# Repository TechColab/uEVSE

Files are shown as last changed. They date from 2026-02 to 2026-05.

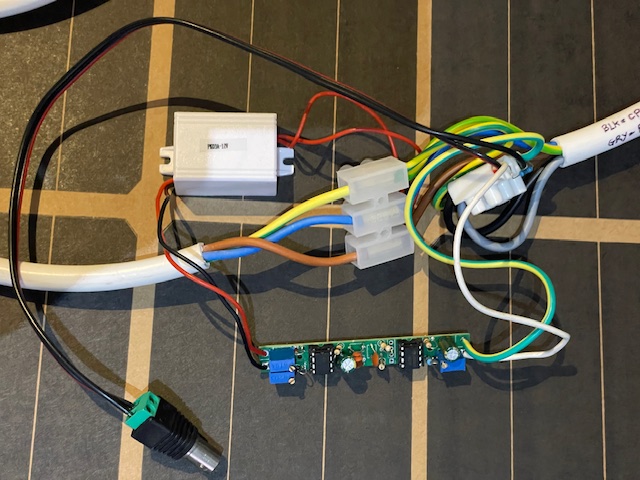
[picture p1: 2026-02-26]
EVSE-components.JPG

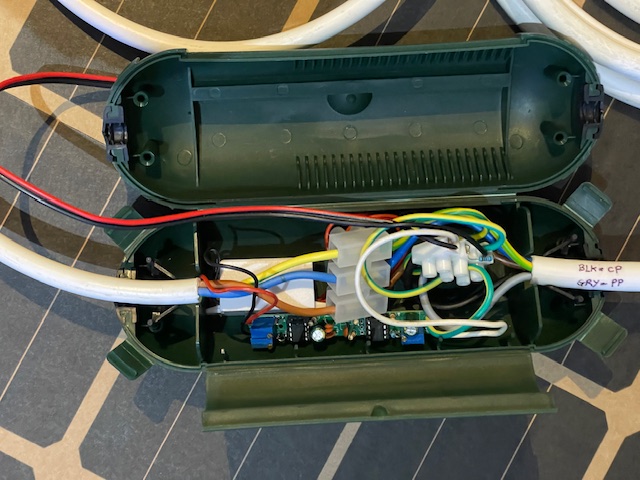
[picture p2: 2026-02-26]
InlineEnclosure.JPG

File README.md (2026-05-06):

# uEVSE or dumb little charger
The minimally viable Electric Vehicle Supply Equipment. Mostly out of curiocity but also as a reaction to the relatively high prices of the cheapest available "Granny charger" products that might be your first step when charging your first BEV.  

In my exploration, the highest unavoidable component costs are the power cable and special connectors. You won't have much choice for the connectors and you really shouldn't compromise on the power cable either. When comparing prices, be sure they are the length you need with a safe amount of slack.  

I've seen quite a few Arduino based DIY EVSE projects but that still has an entry-level threshold of complexity that might put some people off. And I was confident I could make something better - in terms of minimalism.  

Staring with the excellent work by Julian Ilett (JI) at https://www.youtube.com/watch?v=wdK0bfTGi6M&t=7s and other videos, I wanted to address the two biggest issues standing in the way of further simplification.  

The CP (Control Pilot) signal needs to be +/-12V or 24V peak-to-peak.  
In the above example this is acheived with a pair of small 12V batteries which you won't find in your local supermarket. 
Some others have used a dual output PSU with +12V & +5V for the electronics, with a DC-DC converter to generate -12V. 
Another example used 3 separate PSUs.  

I have used a single 12V PSU with the output swing acheived by an H-bridge configuration. 
This takes advantage of the fact that the PE (Protective Earth) of the car & the Earth from the mains, are not related to the 0V power rail of the electonics. This does mean than a fully isolated PSU is an ABSOLUTE requirement but it should be anyway. 
In practice, I bought the 3 cheapest different designs of 12V PSU modules from AliExpress and all were good enough. Two were under GBP 2.00  

The CP signal also needs to follow a multi-stage protocol sequence to make the car happy enough to start drawing current.  
As JI noted, his car was pretty tolerant of the sequence and a definitive specification for the timing of the sequence stages cannot be found online anyway. This made me wonder how much more of the protocol sequence could be skipped. 
I have since succeded without a microcontroller at all, using just a 555 timer & an op-amp with a few resistors & capacitors. 

## Design decisions  
I quickly decided I was going to follow two different paths - the pure minimal and the feature-ritch minimal in the same project. The goals for this version are:  
Drop the option for vented charging such as AGM batteries in golf buggies.  
Cheapest possible entry level that delivers the minimum viable function.  
Fixed output at a modest rate no more than 10A.  
Must connect to car before mains and disconnect mains before car.  
An upgrade path that doesn't waste earlier purchases.  
Not an end product but a kit to educate, and for those willing, form the base of their own functioning DIY EVSE.  

## Experimental evolution  
Following the spec. at  https://en.wikipedia.org/wiki/SAE_J1772  my first thought regarding the 1kHz CP signal was that "you could probably do that with a 555" as it can run directly from 12V. 
I calculated that the maximum current needed from the CP signal is less than 20mA, if we drop the vented charging option. This is within the capability of an NE555P timer chip. But that only has one output when I need a complimentary pair of outputs to get a 24V swing from the 12V supply. A single buffer transistor wouldn't do as the output needs to both sink and source 20mA. I settled on using a cheap op-amp that suits.  

The H-bridge output worked fine on my oscilloscope so I moved on to the next issue of duty cycle. I've never explored the duty-cycle quirks of the 555 so I did some research and found a circuit which allows extreme adjustment from 5 to 95% while also solving the issue of maintaining the frequency while adjusting the duty-cycle. I selected passive components and trim-pots for frequence & duty.  

The first experiments with my car took a bit of manual fidelity but worked in both getting the car to draw some current and learning about the car's protocol expectations. Specifically:  
It did pay attention to the PP (Proximity Pilot) resistor being there (as JI found).  
It didn't seem to care if the mains was presented too early (as JI found).  
It didn't seem to like the 1kHz CP signal being present from the start.  
It does respond to the duty cycle as expected.  
I would like to find the minimum duty cycle the car will work at but I haven't yet.  
I did find that if the duty cycle is accidentally inverted, the 87% presented will cause the car to draw more than enough to trip my home battery before blowing the 13A fuse in the mains plug.  If you're in a country where the mains plugs don't include a fuse, take appropriate precautions.  

While waiting for the special conectors to arrive from China, I bought the cheapest EVSE product I could find which included a timer function to make use of my over-night tariff. Disappointingly it can set a delay or a duration but not both. I later discovered that after a power-loss, it will return to the last used charge current and carry on. So I tried it via a Smart-switch rated at 16A and found it works fine with a schedule configred from the mobile app. I could have bought an EVSE without the built-in timer function. In fact this is the key to the cost-efficient upgrate path.  

By looking at the signals from the bought EVSE on my oscilloscope, I thought my circuit probably needed the CP to be held at 12V+ for an initiual period before starting the 1kHz square wave. As I used an LM358 dual op-amp chip, I could use the spare to hold the 555 in reset until a capacitor charged through a resistor, giving a couple of seconds delay. This breadboard prototype sucesfully got the car to draw a controlled amount of current shortly after boot. Proof of concept!  

As an early experiment for the feature-ritch varient, I also tried it with a 4428 driver IC to see if that would help square-off the rather imperfect signal edges. It didn't make much difference but the driver got rather hot. This was a dual complimentary pair package where I was initially driving both inputs from the 555 so they had a brief cross-over period. I later tried a 4423/4424 dual matched pair package where one was driven from the 555 and the other from the output of the op-amp inverter whose propogation delay was enough to avoid the over-lap heating.  

At this point I designed a PCB which would fit within a single-module DIN rail enclosure and ordered 5. While awaiting delivery, I did more testing and found the 555's timing to be pretty unstable. I programmed an Arduion to measure the mark and space periods from its interrupt pin and build up some statistics over an 8-hour period. It was quite alarming. I hoped this was mostly caused by the breadboard wiring as my PCB didn't have space for any ground plane.  

Upon receiving the PCBs, I populated one with decent quality pin-through-hole (PTH) passives and good sockets for the ICs. It worked better than the breadboard prototype did but hardly rock-steady. It took quite a while to trim the pots for a 13% duty cycle at 1kHz. I found it best to set the frequency pot to its centre then parallel timing capacitors to get it into the ball-park before trimming in. I found the car wouldn't stay charging for very long, even if I trimmed the 555 to start around 990Hz so that it was still below 1100Hz after settling.  

Having fitted the PCB into a 1-mod DIN rail enclosure, I can see that an hour-glass shapped PCB would have a bit more space. Switching to surface-mount-devices (SMD) should enable enough space for a ground plane while also allowing better quality components. But this would detract from the DIY-friendly aims. Meanwhile the Rev 0.2 PCB design is a mid-way improvement which allows the CP signal pair to be sent to and/or returned from a daughter board to either buffer or bypass the analogue ICs.   

I think this is another case which shows that the 555 isn't really that good at basic timing! To know if this task is really beoyond the 555's capabilities, I need to further explore the timing tolerances of my car, with some accuracy. Probably the beast way to do this would be to build the feature-ritch variant anyway!  

## Feature ritch varient  
I have used an ESP-01 in place of a 555 before so it seems a natural choice here. The pros and cons being as follows:  
 * pro Hopefully more accurate timing  
 * pro Better duty-cycle control: 0-100% without any impact on frequency  
 * pro Allows real-time control by mobile device, for duty-cycle, on/off, delay-start, duration-limit etc.  
 * pro Potential integration with Home Assistant etc.  
 * pro Easier to build the hardware  
 * pro Does not need the op-amp  
 * con Needs driver IC with 3.3V inputs and 12V outputs  
 * con Needs a 3.3V supply regulator  
 * con Very limited outputs, in terms of count and restrictions  
 * con Needs software development  
Probably about the same size and cost.  

## ESP_EVSE first test  
My mini ESP-01 prototype carrier board was ideal for this with the addition of a 3-pin 3.3V miniature DC-DC regulator and a couple of capacitors. I use the ESP-01S pin2 for the CP and pin1 for the complimentary PE after a deadband delay. It was a simple sketch with some serial debug then a loop of four delayMicroseconds() calls. This was immdiately more stable than the 555. I just added a 4424 driver IC to the patch-bay area and the 1k resistor at the output to get it working. There are still the occasional drawn-out delays and it took a while to get the frequency and duty right but I was confident enough to leave it on over-night. I had the duty set for about 6A and after 6h50m on the cheap tariff it had charged 8.89kWh. A success.  

## ESP_EVSE feature build-out  
Uses hardware timer interupts for much more stable signal. Can use webapp on mobile to change the duty-cycle while it's running. Has place-holders for start-delay and charge-duration. Settings saved in flash and loaded at boot. Captive AccessPoint to set your WiFi. Over-The-Air update needs testing. Yet to test lowest duty-cycle. Need to re-check it runs as expected from cold power-on. Much tidying to do, like making UI based on Amps translated to duty-cycle. Make the button do something. 

## ESP_EVSE more tweaks  
The mDNS doesn't seem to be working so I have used the double-boot to blink our IP address (last byte). UI now sets current in Amps and code converts to duty-cycle. Output is now on GPIO1 & GPIO3 to free-up GPIO2 for blinking the new setting on each change.  

## ESP_EVSE minimum test  
I have wondered what the minimum power deliver is so I could considere a portable PV kit. The EVSE I bought doesn't go below 8A and I have read that there seems to be an unofficial minimal current limit of 6A. Now my DIY ESP_EVSE has live update by web-page, it was easy to test. My car will happily take 6A but if I set the duty-cycle to dictate a current limit of 5A, the car stops charging. After upping the limit to 6A again, the car started charging again. It would be interesting to know if the 6A limit is the same at lower voltages - E.g. 120V. My mains is often over 240V but assuming it works at 220V, that would be a minimum input of 1320W. Even if the same limit applies at 110V, that would mean the smallest portable generators of 600W would be too little. However, you should be able to run a common 2kVA generator at less than full throttle.  

## published  
And added an initial PCB design for the ESP_EVSE.  

## ESP_EVSE overnight test  
During the minimum current test, The power monitoring smart socket showed the drawn current would vary a bit, perhaps related to variations in mains voltage among other things. This made me wonder if that was enough to make the car stop & start charging each time it dipped below 6A. So last night I put it on the timer for 00:10am till 05:50am at 6A set by the GUI. It started just below 6A but it did start. This morning I checked and it was drawing 5765mA at 237.6V until it stopped with a total of 8.94kWh logged. 8.94kWh / 6.67hours =~ 1341W  and  1341W / 237.6V =~ 5644mA  so the minimum is below 6A but above 5A. That's close enough for me.  

Getting the current would enable an self-regulating mode where it could slowly decrease the duty-cycle until the car stops drawing, then increase again, while calculating a reliable averagee setting to just avoid drop-outs. This doesn't seem worth the effort. But I will start a simple list of cars and their discovered limits to see if this might be useful for others.

A better use for knowing the current would be to optionaly stop the EVSE when the car reduces its draw below a certain amount. I.e. stop before full to preserve the battery's long-term health. My car has NMC chemistry so this would be nice. I would need to do full logging of the current over time as the car is charged to 100% with an EVSE setting of perhaps 10A. But at such a low current, it's possible that the car might only back-off its draw when it is so close to 100% that there's no significat difference.

In either case I would need the ESP to know the curent. It doesn't have enough pins (without upgrading to a different module) but it could potentially read the current by WiFi from the smart plug. I will investigate further. Meanwhile I have ordered some hall-effect switches to test on the button. 
 
## End times  
I've just charged the car to 100% for the first time with the ESP_EVSE and 5 minutes before the end of the cheap rate, I checked the current on the smart-switch. It was a little over 4A so a significant enough drop to be detected and used. I will have to get some logging to chart how long before full it backs-off. A good excuse to finally get round to Home Assistant. If the drop from 6A is too close to 100% then I could perhaps try something like every 15 minutes, doing a 30 second burst of PWM offering 12A to see what the car does before returning to 6A. If the car draws less than 12A, then I would note what it did draw, and stop charging. Then check on the car's state of charge. 

## To do  
Need to change the setting so we dial to desired number, then comit. Rather than setting to each number on the way. 
The pin0 button (for programming) is still usable for user interaction, possibly via magnetic hall-switch to maintain IP65.  
I'm aware of the security implications, so I could use pin0 to ensure that the web interface is ignored unless a magnet is present.  
I will look into the LED pin usage. If there is stil a pin free, then I would put an addressable RGB LED on it, for user feedback.  
Add support for remote control like Home Automation.  
To be continued.

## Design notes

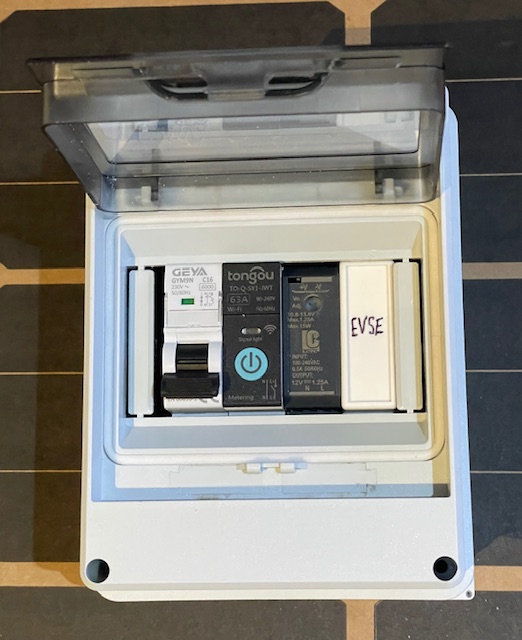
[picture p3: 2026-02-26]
RCBO+SmartBreaker+PSU+EVSE.jpg

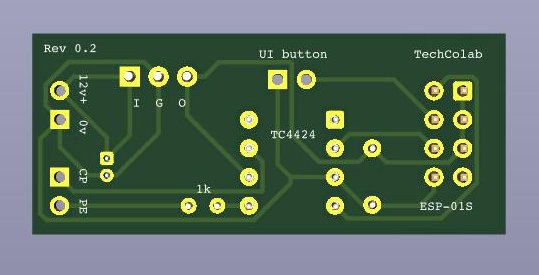
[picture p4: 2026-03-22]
ESP_EVSE-B.jpg

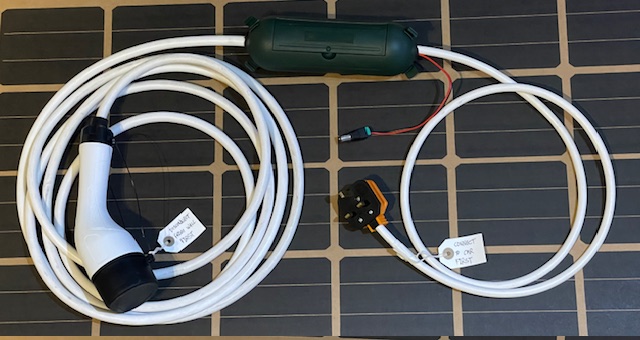
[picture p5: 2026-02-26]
EVSE-InlineEnclosure.jpg

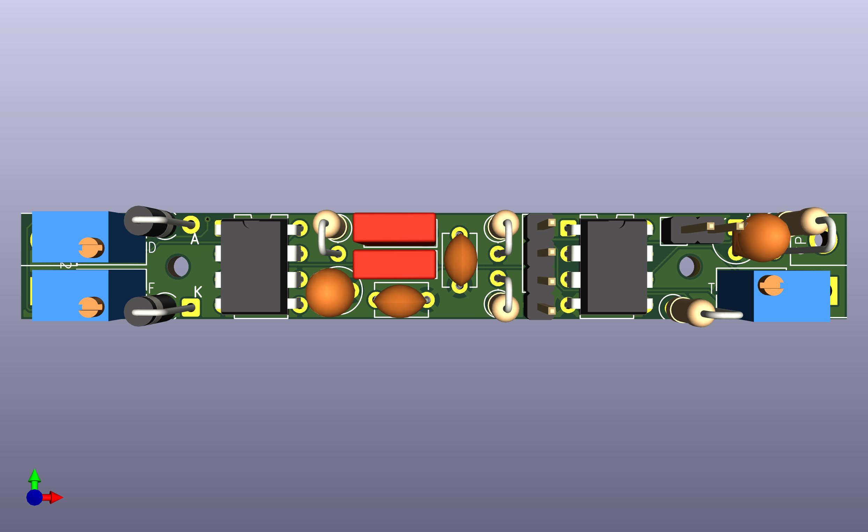
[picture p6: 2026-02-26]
uEVSE-F.jpg

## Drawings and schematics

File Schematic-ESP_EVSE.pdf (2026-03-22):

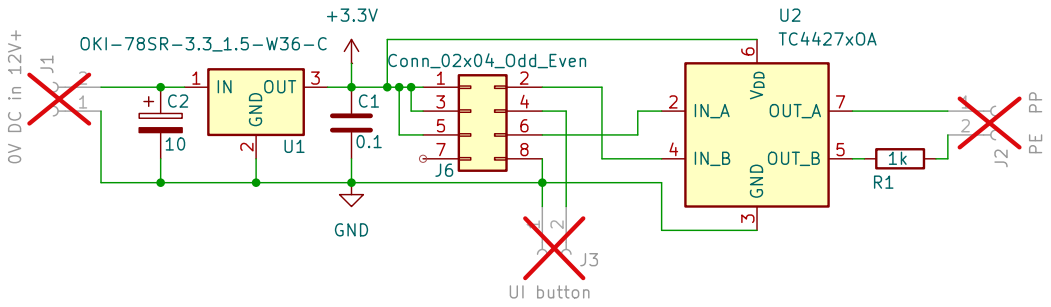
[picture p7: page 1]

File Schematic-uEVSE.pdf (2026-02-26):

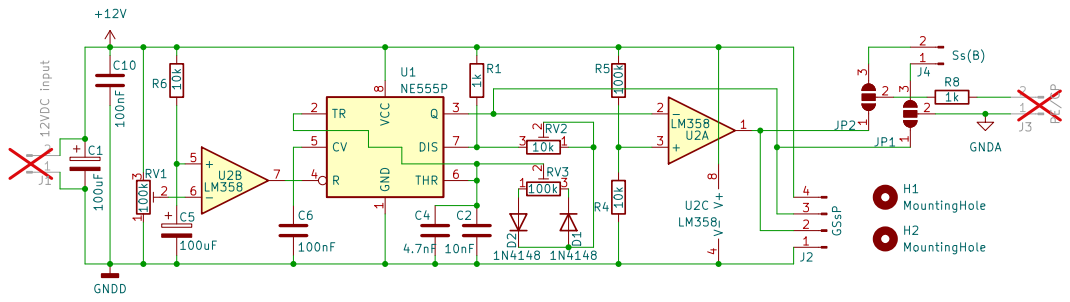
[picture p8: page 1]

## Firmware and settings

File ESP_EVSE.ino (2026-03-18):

#define TRUE (0==0)
#define FALSE (0!=0)

#include <LittleFS.h>
#include <WiFiManager.h> // tzapu
#include <ArduinoJson.h>
#include <ESP8266WiFi.h>
#include <ESP8266WebServer.h>
#include <ESP8266mDNS.h>
#include <ArduinoOTA.h>
#include <ESP_DoubleResetDetector.h>
#include <ESP8266TimerInterrupt.h>

// Configuration variables
int cfg_int = 0;
float cfg_float = 0.0;
String cfg_str = "";
float prv_float = 0.0;
const int LED_PIN = 2; // Built-in LED for ESP-01S (GPIO2)
const int CP_pin = 3;
const int PE_pin = 1;
const String ver = String(__DATE__) + " " + String(__TIME__);
const int debug = FALSE;

// Pulse timing in microseconds
float duty = 10.0;
uint32_t deadband = 3 * 5;
uint32_t correction = 18; // taken from both sides
uint32_t period = (1000 - correction) * 5; // uS 1000000 * (1/freq)ISR_PE_HI
float k = period / 100.0;
uint32_t mark = floor((duty * k) - correction);
uint32_t space = period - mark - correction;

ESP8266WebServer server(80);
DoubleResetDetector* drd;

void ICACHE_RAM_ATTR ISR_CP_LO();
void ICACHE_RAM_ATTR ISR_PE_HI();
void ICACHE_RAM_ATTR ISR_CP_HI();
void ICACHE_RAM_ATTR ISR_PE_LO();

void ICACHE_RAM_ATTR ISR_CP_LO()
{
  timer1_detachInterrupt();
  digitalWrite(CP_pin, LOW);
  timer1_write(deadband); timer1_attachInterrupt(ISR_PE_HI);
}

void ICACHE_RAM_ATTR ISR_PE_HI()
{
  timer1_detachInterrupt();
  digitalWrite(PE_pin, HIGH);
  timer1_write(space - deadband); timer1_attachInterrupt(ISR_CP_HI);
}

void ICACHE_RAM_ATTR ISR_CP_HI()
{
  timer1_detachInterrupt();
  digitalWrite(CP_pin, HIGH);
  timer1_write(deadband); timer1_attachInterrupt(ISR_PE_LO);
}

void ICACHE_RAM_ATTR ISR_PE_LO()
{
  timer1_detachInterrupt();
  digitalWrite(PE_pin, LOW);
  timer1_write(mark - deadband); timer1_attachInterrupt(ISR_CP_LO);
}

// Save variables to LittleFS
void saveConfig() {
  StaticJsonDocument<256> doc;
  doc["cfg_int"] = cfg_int;
  doc["cfg_float"] = cfg_float;
  doc["cfg_str"] = cfg_str;

  File file = LittleFS.open("/config.json", "w");
  if (file) {
    serializeJson(doc, file);
    file.close();
    Serial.println("Config saved to flash.");
  }
}

// Load variables from LittleFS
void loadConfig() {
  if (LittleFS.exists("/config.json")) {
    File file = LittleFS.open("/config.json", "r");
    StaticJsonDocument<256> doc;
    DeserializationError error = deserializeJson(doc, file);
    if (!error) {
      cfg_int = doc["cfg_int"] | 0;
      cfg_float = doc["cfg_float"] | 0.0;
      cfg_str = doc["cfg_str"].as<String>();
    }
    file.close();
  }
}

// Throb LED logic for visual feedback
void throbLED(int count) {
  for (int i = 0; i < count; i++) {
    for (int v = 255; v >= 0; v--) { analogWrite(LED_PIN, v); delay(2); }
    for (int v = 0; v <= 255; v++) { analogWrite(LED_PIN, v); delay(2); }
  }
}

void blinkNumber(int num) {
  if (num == 0) {
    // Blink 10 times for '0'
    for(int i=0; i<10; i++){
      digitalWrite(LED_PIN, LOW); delay(100);
      digitalWrite(LED_PIN, HIGH); delay(100);
    }
  }
  for (int i = 0; i < num; i++) {
    digitalWrite(LED_PIN, LOW); delay(200);
    digitalWrite(LED_PIN, HIGH); delay(200);
  }
  delay(1000); // Pause between digits
}

void setup() {
  Serial.begin(115200, SERIAL_8N1, SERIAL_TX_ONLY); delay(600); Serial.printf("\n\n\n");
  pinMode(LED_PIN, OUTPUT);
  digitalWrite(LED_PIN, HIGH); // LED Off (Active Low)

  drd = new DoubleResetDetector(20, 0x00);
  LittleFS.begin();
  loadConfig();
  duty = cfg_float /0.6 ;

  WiFiManager wm; // WiFi Captive Portal
  if (!wm.autoConnect("ESP-EVSE-Config")) {
    Serial.println("Failed to connect, restarting...");
    ESP.restart();
  }

  if (!MDNS.begin("ESP-EVSE")) {
    Serial.println("Error setting up MDNS responder!");
  } else {
    MDNS.addService("http", "tcp", 80);
  }

  // Handle Double Reset (Factory Reset)
  if (drd->detectDoubleReset()) {
    Serial.println("Double Reset Detected! blinking IP...");
    IPAddress ip = WiFi.localIP();
    blinkNumber(ip[3] / 100);
    blinkNumber((ip[3] / 10) % 10);
    blinkNumber(ip[3] % 10);
  }

  ArduinoOTA.begin();

  // --- WEB SERVER ROUTES ---MDNS.addService("http", "tcp", 80)

  server.on("/", []() {
    String html = "<h1>ESP-EVSE Home</h1><p>FW Date: " + ver + "</p>";
    html += "<p><a href='/app'>Configure Variables</a></p>";
    html += "<script>fetch('/settime?t='+Math.floor(Date.now()/1000));</script>";
    server.send(200, "text/html", html);
  });

  server.on("/app", []() {
    String html = "<html><head><meta name='viewport' content='width=device-width, initial-scale=1'>";
    html += "<style>body{font-family:sans-serif;padding:20px;max-width:400px;margin:auto;} .row{margin:25px 0;} button{padding:10px 15px;} ";
    html += ".warn{background:#ff4444; color:white; border:none; width:100%; margin-top:40px; padding:15px;}</style></head><body>";
    html += "<h2>Settings</h2>";
    html += "<div class='row'><b>Int:</b> <button onclick='chg_i(-1)'>-</button> <span id='val_i'>" + String(cfg_int) + "</span> <button onclick='chg_i(1)'>+</button></div>";
    html += "<div class='row'><b>Float:</b> <button onclick='chg_f(-1.0)'>-</button> <span id='val_f'>" + String(cfg_float) + "</span> <button onclick='chg_f(1.0)'>+</button></div>";
//  html += "<div class='row'><b>Float:</b> <br><input type='range' min='0' max='100' step='0.1' style='width:100%' value='" + String(cfg_float) + "' oninput='document.getElementById(\"dis_f\").innerText=this.value' onchange='upd(\"f\",this.value)'><br>Value: <span id='dis_f'>" + String(cfg_float) + "</span></div>";
    html += "<div class='row'><b>String:</b> <br><input type='text' style='width:100%;padding:8px;' value='" + cfg_str + "' onchange='upd(\"s\",this.value)'></div>";
    html += "<button onclick='location.href=\"/save_flash\"' style='width:100%'>Commit to Flash</button>";
    html += "<button class='warn' onclick='if(confirm(\"Clear all settings and Sleep?\"))location.href=\"/factory_reset\"'>Factory Reset & Sleep</button>";
    html += "<script>";
    html += "function upd(p,v){fetch('/update?'+p+'='+encodeURIComponent(v));}";
    html += "function chg_i(d){let e=document.getElementById(\"val_i\"); let nv=parseInt(e.innerText)+d; e.innerText=nv; upd(\"i\",nv);}";
    html += "function chg_f(d){let e=document.getElementById(\"val_f\"); let nv=parseFloat(e.innerText)+d; e.innerText=nv; upd(\"f\",nv);}";
    html += "</script></body></html>";
    server.send(200, "text/html", html);
  });

  server.on("/update", []() {
    if (server.hasArg("i")) cfg_int = server.arg("i").toInt();
    if (server.hasArg("f")) cfg_float = server.arg("f").toFloat();
    if (server.hasArg("s")) cfg_str = server.arg("s");
    server.send(200, "text/plain", "OK");
  });

  server.on("/save_flash", []() {
    saveConfig();
    server.sendHeader("Location", "/app");
    server.send(303);
  });

  server.on("/factory_reset", []() {
    server.send(200, "text/plain", "Formatting and Sleeping...");
    delay(500);
    LittleFS.format();
    throbLED(3);
    ESP.deepSleep(0);  if(debug){ Serial.println("body"); }
  });

  server.on("/settime", []() {
    if (server.hasArg("t")) {
      struct timeval tv = { .tv_sec = (time_t)server.arg("t").toInt() };
      settimeofday(&tv, NULL);
      server.send(200, "text/plain", "OK");
    }
  });

  server.begin();

  // Final Startup Log
  Serial.println("\n--- STARTUP LOG ---");
  Serial.printf("Int: %d\nFloat: %f\nStr: %s\nIP: %s\n", cfg_int, cfg_float, cfg_str.c_str(), WiFi.localIP().toString().c_str());
  Serial.println("-------------------");
  Serial.print("ver ");         Serial.println(ver);
  Serial.print("duty ");        Serial.println(duty);
  Serial.print("correction ");  Serial.println(correction);
  Serial.print("mark ");        Serial.println(mark);
  Serial.print("space ");       Serial.println(space); 
  Serial.print("debug ");       Serial.println(debug); 
  delay(1000);

  if(! debug){
    Serial.end();

    pinMode(CP_pin, OUTPUT);
    pinMode(PE_pin, OUTPUT);
    digitalWrite(CP_pin, HIGH);
    digitalWrite(PE_pin, LOW);
    delay(3000);

    timer1_enable(TIM_DIV16, TIM_EDGE, TIM_SINGLE); // 5 ticks per uS
    timer1_write(31250); timer1_attachInterrupt(ISR_CP_LO);
  }
}

void loop() {
  drd->loop();
  server.handleClient();
  ArduinoOTA.handle();
  MDNS.update();

  if(cfg_float != prv_float){
    blinkNumber(int(cfg_float));
    prv_float = cfg_float;
    duty = cfg_float /0.6 ;
    if(debug){ Serial.println(duty); }
    mark = floor((duty * k) - correction); space = period - mark - correction;
  }
  delay(1000);
}
